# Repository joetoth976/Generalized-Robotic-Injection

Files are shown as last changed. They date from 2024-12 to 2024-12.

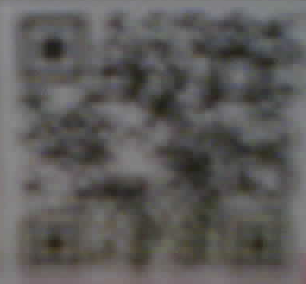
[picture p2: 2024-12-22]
MATLAB/images/datum.png

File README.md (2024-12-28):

# Generalized-Robotic-Injection
https://github.com/user-attachments/assets/c4ef7c3b-5e16-4c82-9615-c5fa265d2843

This repository provides the necessary drawings, code, and instructions to replicate a 3DOF robotic arm capable of simulated automatic injection. The robot utilizes an IP-Camera and ultrasonic sensor to detect injection sites through the MATLAB Computer Vision Toolbox and a control applet. 

## Video Demonstration
[Link to Full Demo](https://uofnelincoln-my.sharepoint.com/:v:/g/personal/jtoth3_unl_edu/ESOxoaJ-kIhIvgtayEl0OS0BzzwsHD2kksnlrYsa-0oggw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)

## Components
| Item | Manufacturer/Link | Price |
| --- | --- | ----- |
| 6-DOF Robotic Arm Kit | [Diymore/Amazon](https://www.amazon.com/diymore-Aluminium-Mechanical-Robotic-Arduino/dp/B01LVVEP8K) | $50 |
| Arduino MEGA 2560 | [Elegoo](https://us.elegoo.com/products/elegoo-mega-2560-r3-board) | $20 |
| 16-Channel Servo Shield | [Adafruit](https://www.adafruit.com/product/1411) | $17 |
| ESP32-IPCamera | [ai-thinker](https://www.amazon.com/Aideepen-ESP32-CAM-Bluetooth-ESP32-CAM-MB-Arduino/dp/B08P2578LV)| $10 |
| HC-SR04 Ultrasonic Sensor | [Adafruit](https://www.adafruit.com/product/4007) | $4 |
| 5V DC Power Adapter | [Waysse](https://www.amazon.com/Adapter-100V-240V-Charger-Speaker-Devices/dp/B08Z7GNDKT) | $8 |
| Micro-USB Power Cable | [MYFON](https://www.amazon.com/Charging-Transfer-Android-Trustable-MYFON/dp/B098DW7485) | $6 |
| Jumper Wires | [Elegoo](https://www.amazon.com/Elegoo-EL-CP-004-Multicolored-Breadboard-arduino/dp/B01EV70C78) | $7 |
| Electrical Tape | [Scotch](https://www.amazon.com/Scotch-Electrical-Tape-4-Inch-66-Foot/dp/B001ULCB1O) | $4 |
| | **Total:** | **$126** |

## MATLAB
[Download & Install MATLAB](https://www.mathworks.com/help/install/ug/install-products-with-internet-connection.html)

Include the following toolboxes:
[Computer Vision Toolbox](https://www.mathworks.com/products/computer-vision.html), [MATLAB Support Package for IP Cameras](https://www.mathworks.com/matlabcentral/fileexchange/49824-matlab-support-package-for-ip-cameras)

Download the entire MATLAB folder from this repository. Set the current file in MATLAB as the downloaded folder. Reconfigure the MATLAB control applet's code to suit your project's needs and repackage it as an app as needed. 

## Arduino
[Download & Install Arduino IDE](https://www.arduino.cc/en/software)

Download the arm_command.ino file and upload it to the Arduino MEGA 2560 via Arduino IDE. 

## Integration
Follow the directions, schematics, and software descriptions laid out in the Project Overview document. 

## Acknowlegements
This project utlized the robotic kit and [control software](https://github.com/smrLab/Robotic-Arm-Kit) from the [Smart Materials and Robotics Laboratory](https://smr.unl.edu/) at the [University of Nebraska-Lincoln Department of Mechanical and Materials Engineering](https://engineering.unl.edu/mme/). 

The following Arduino Libraries were used: [Adafruit PWM Servo Driver Library](https://github.com/adafruit/Adafruit-PWM-Servo-Driver-Library), [HC-SR04 Library](https://github.com/Martinsos/arduino-lib-hc-sr04)

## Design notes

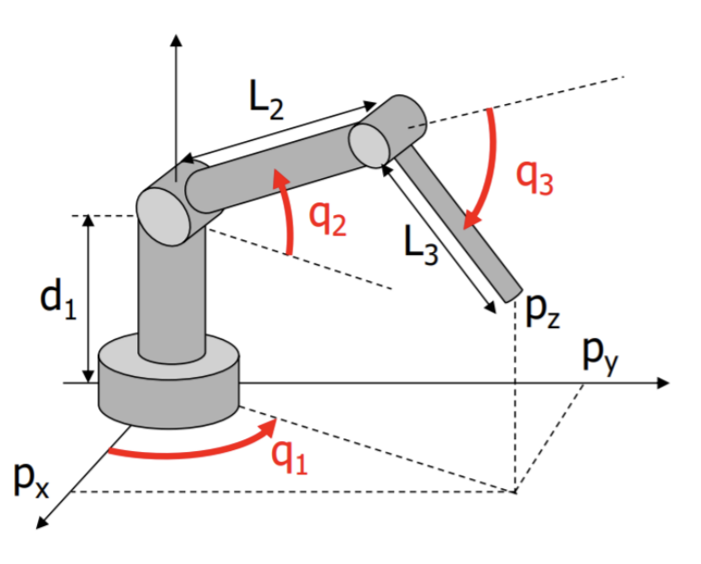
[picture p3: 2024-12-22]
MATLAB/images/Screenshot 2024-11-15 at 1.43.06.png

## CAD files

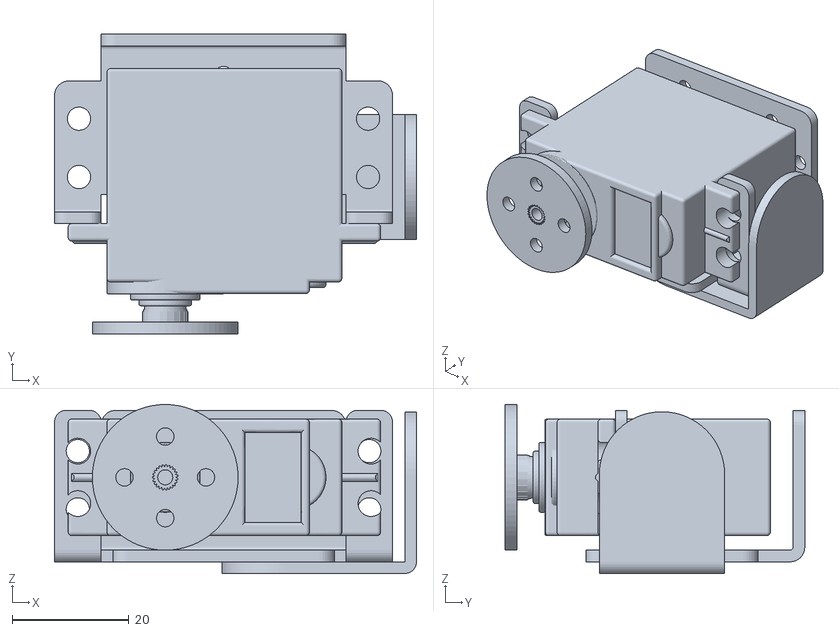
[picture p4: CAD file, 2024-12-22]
MATLAB/3d models/link3.stl
62.1 x 51.4 x 29.0

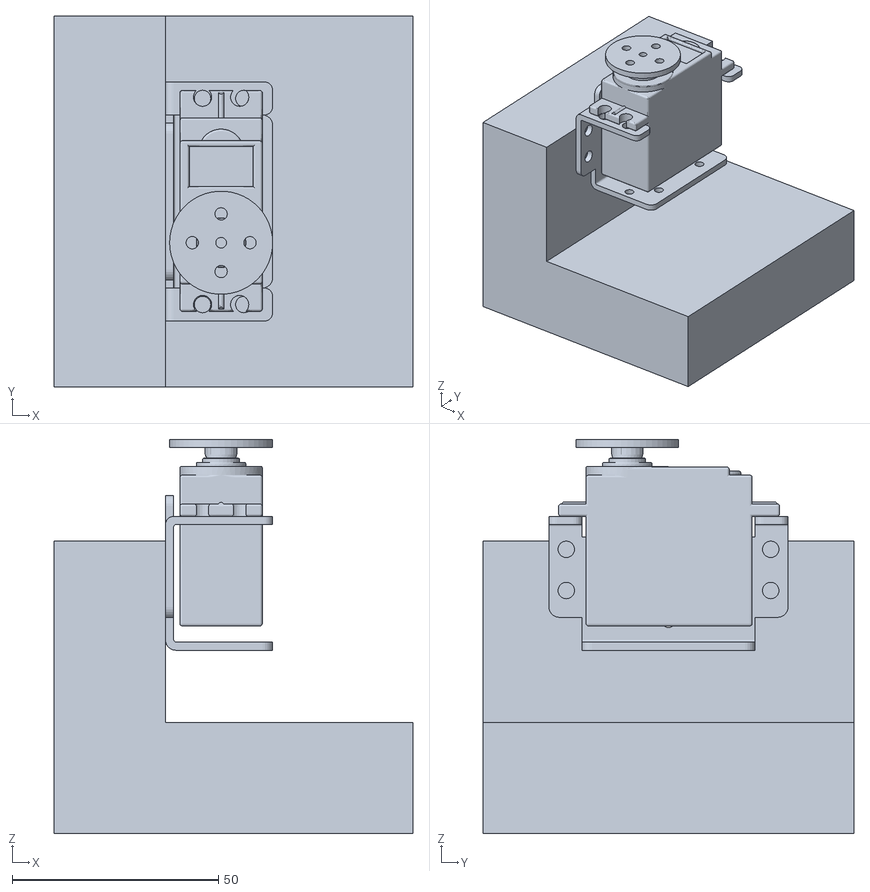
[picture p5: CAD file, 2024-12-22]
MATLAB/3d models/base.stl
87.0 x 90.0 x 95.7

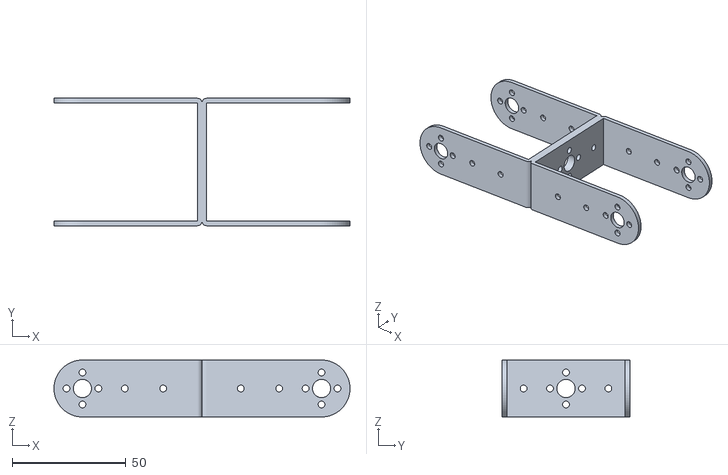
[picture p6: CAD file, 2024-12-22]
MATLAB/3d models/link2.stl
130.0 x 56.0 x 25.0

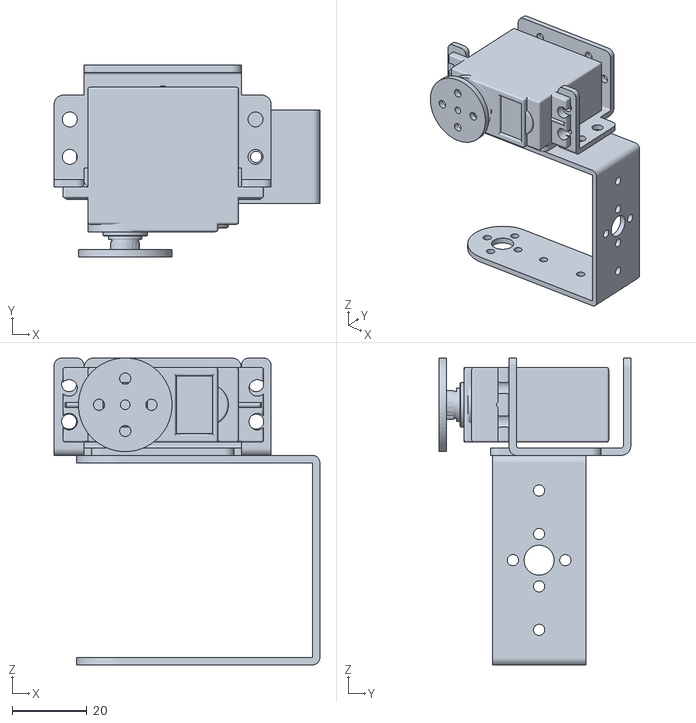
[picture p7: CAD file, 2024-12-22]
MATLAB/3d models/link1.stl
71.0 x 51.2 x 82.0

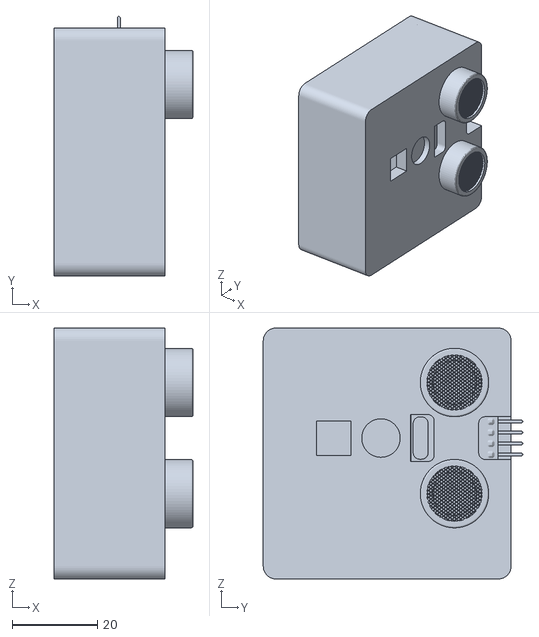
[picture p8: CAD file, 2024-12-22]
MATLAB/3d models/ee.stl
32.5 x 60.7 x 58.7

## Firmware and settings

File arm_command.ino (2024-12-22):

#include <Wire.h>
#include <Adafruit_PWMServoDriver.h>
#include <HCSR04.h>

Adafruit_PWMServoDriver pwm = Adafruit_PWMServoDriver();
UltraSonicDistanceSensor distanceSensor(22, 23);
#define SERVO_FREQ 50 // Analog servos run at ~50 Hz updates

String incomingString = "0";
int typeString = 0;
String dataString = "0";
int type = 0;
int pwmv = 0;
int q1 = 0;
int q2 = 0;
int q3 = 0;

void setup() {
  // Initialize serial communication 
  Serial.begin(115200);
  // Initialize pwm communication
  pwm.begin();
  // Set onboard oscillator frequency
  pwm.setOscillatorFrequency(24000000);
  pwm.setPWMFreq(SERVO_FREQ);  
  delay(10);
}

void loop() {
  if (Serial.available() > 0) { 
    incomingString = Serial.readStringUntil('\n');
    typeString = incomingString.substring(0,1).toInt();
    dataString = incomingString.substring(1);
    switch (typeString) {
      // Configure Command
      case 1:  
        type = dataString.substring(0,1).toInt();
        pwmv = dataString.substring(1,4).toInt();
        if (type==1){
          pwm.setPWM(0,0,pwmv);
        }
        if (type==2){
          pwm.setPWM(1,0,pwmv);
        }
        if (type==3){
          pwm.setPWM(2,0,pwmv);
        }
        break;

      // Point Command
      case 2:  
        q1 = dataString.substring(0,3).toInt();
        q2 = dataString.substring(3,6).toInt();
        q3 = dataString.substring(6,9).toInt();
        pwm.setPWM(0,0,q1);
        pwm.setPWM(1,0,q2);
        pwm.setPWM(2,0,q3);
        break;

      // Point Command & Distance Send
      case 3:  
        q1 = dataString.substring(0,3).toInt();
        q2 = dataString.substring(3,6).toInt();
        q3 = dataString.substring(6,9).toInt();
        pwm.setPWM(0,0,q1);
        pwm.setPWM(1,0,q2);
        pwm.setPWM(2,0,q3);
        Serial.println(distanceSensor.measureDistanceCm());
        break;
    }
  }
}
